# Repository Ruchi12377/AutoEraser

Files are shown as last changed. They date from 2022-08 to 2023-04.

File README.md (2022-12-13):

# 自動ホワイトボード消しの実用化に向けた改良

## 2022/12/13 第4版発行

---

# 目次

1. はじめに
   
   1. 概要
   
   2. 開発環境
   
   3. システムの概要

2. コンポーネント
   
   1. Camera
   
   2. Image
   
   3. KeystoneCorrection
   
   4. WhiteBoard (Feature)
   
   5. Select
   
   6. Erase (Feature)
   
   7. MoveInitial
   
   8. InitialSetting
   
   9. Pump
   
   10. Move (Feature)
   
   11. Serial

# 1.はじめに

## 1.概要

我々はRTミドルウェアを用いて、ホワイトボードの文字を自動で消すシステムを開発している。本稿では、本システムの改善について述べる。昨年のシステムとの相違点は主に三点ある。一つ目は、材質を木材からアルミニウムに変更することで歪みを解消し、スムーズな可動と軽量化を図ったことである。二つ目は消したい領域をより細かく指定可能にすることで、本来消すべきではない部分を消してしまうことを防げるようになったことである。三つ目は水が入ったタンクを設置し、自動で白板を濡らすことができるようになったため、雑巾を取り外して濡らす必要がなくなったことである。

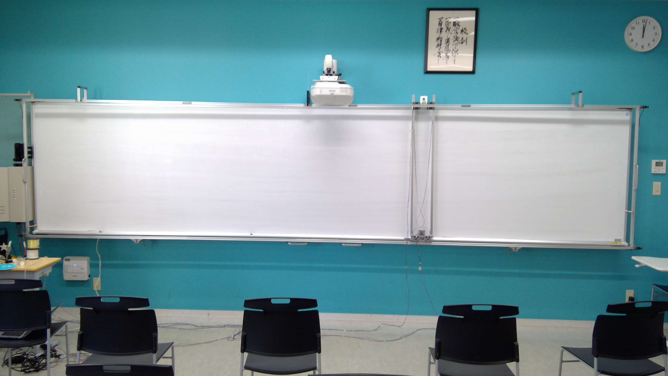
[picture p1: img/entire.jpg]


自動ホワイトボード消しのイメージ

## 2.開発環境

本コンポーネント群の開発環境を以下に示す。

| OS | Windows10 |
| --- | --- |
| RTミドルウェア | OpenRTM-aist-2.0.0-RELESE(Python 版) |
| 開発環境 | VSCode |
| Python | 3.8.5 |
| 必要モジュール  | math, numpy, cv2, PIL, sys, time, tkinter |

## 3.システムの概要

このシステムは、ユーザーの指定した範囲もしくは、全範囲(全部消す)をレールや枠組みに沿って本体が移動し自動でホワイトボードに書かれたものを消すものである。

そして、制御部分にはRTミドルウェアを用いており、Cameraコンポーネントを用いて取得したホワイトボードの動画(画像)をSelectコンポーネントで消す範囲を選択し、Eraseコンポーネントでどのように移動するか決定することでMoveコンポーネントが移動するためのコマンドを生成し、Serialコンポーネントを用いてハードウェアに移動するデータをもちいて実際に動かす。というものである。

以下の2つのコンポーネント図を示す。

1.詳しく説明してあるコンポーネント図

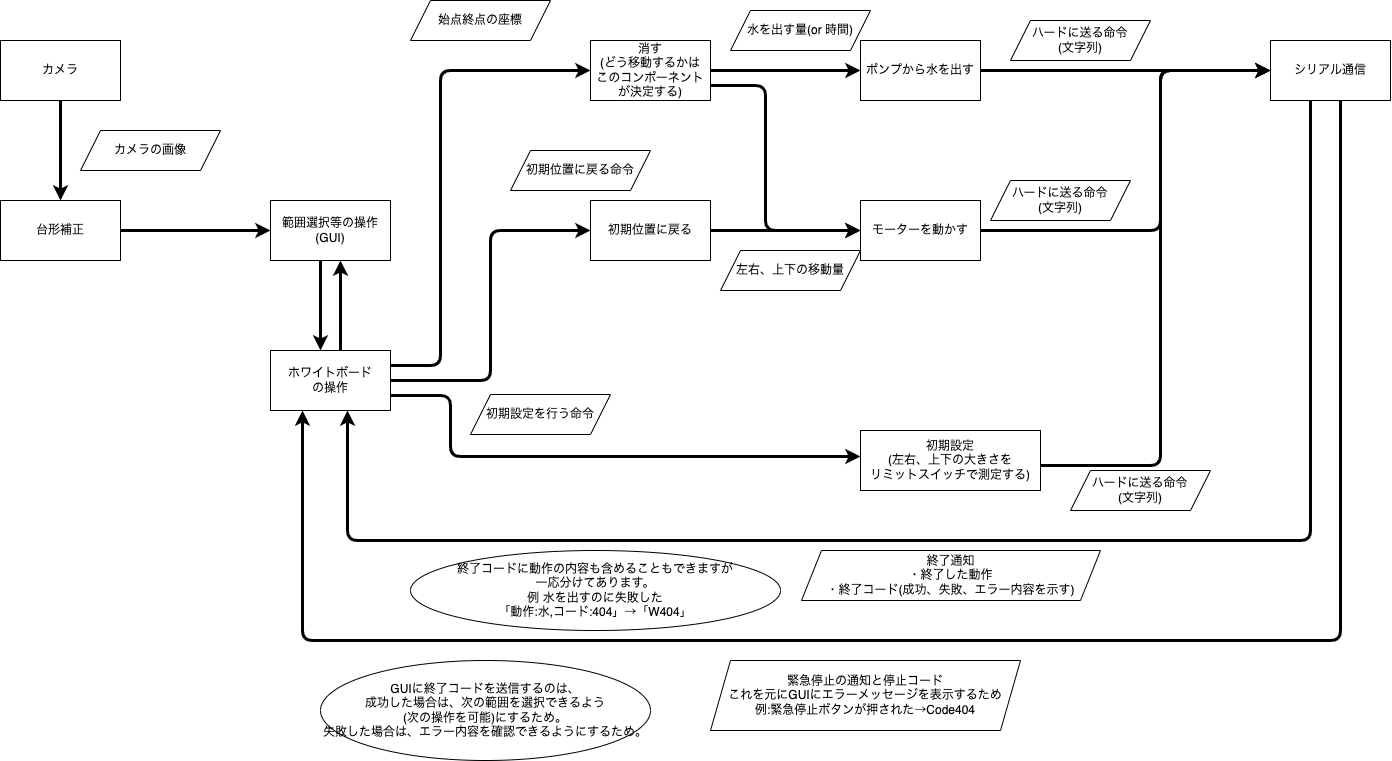
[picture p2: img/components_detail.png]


2.簡潔化しまとまりごとに色分けしたコンポーネント図

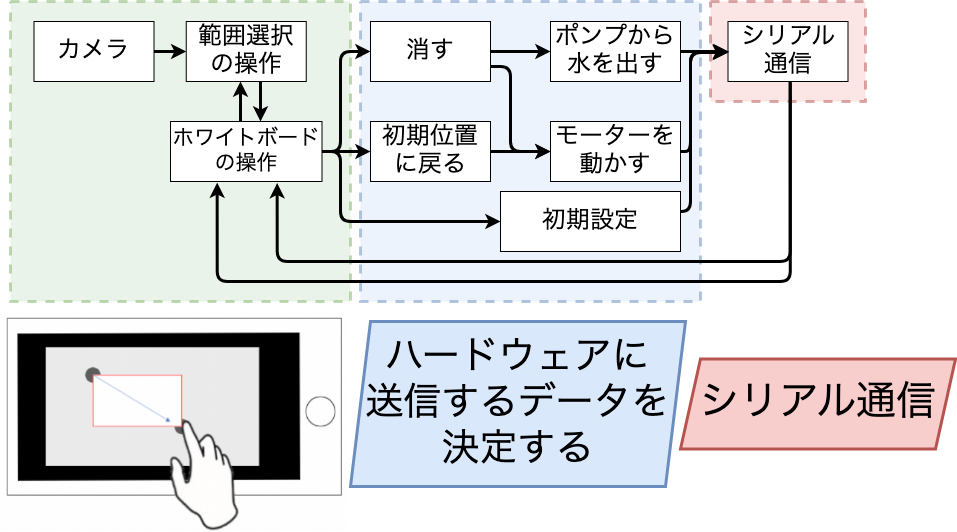
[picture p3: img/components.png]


# 2.コンポーネント

## 1.Camera

カメラから取得した画像を出力するコンポーネント。

コンフィギュレーションから使用するカメラのインデックスを設定することができる。

- **InPort**

- **OutPort**
  
  | **名称** | **データ型**         | **説明**            |
  | ------ | ---------------- | ----------------- |
  | image  | RTC::CameraImage | カメラから取得した画像を出力する。 |

- Configuration
  
  | 名称          | データ型  | 説明                   | 初期値 | 制限      |
  | ----------- | ----- | -------------------- | --- | ------- |
  | CameraIndex | short | 使用するカメラのインデックスを設定する。 | 0   | 0<=x<=5 |

## 2.Image

コンフィギュレーションで指定されたパスの画像をポートから出力するコンポーネント。

デバックする際、Cameraコンポーネントの代わりに使用することを想定している。

- **InPort**

- **OutPort**
  
  | 名称    | データ型             | 説明                           |
  | ----- | ---------------- | ---------------------------- |
  | Image | RTC::CameraImage | コンフィギュレーションで指定されたパスの画像を出力する。 |

- **Configuration**
  
  | 名称   | データ型   | 説明        | 初期値          | 制限        |
  | ---- | ------ | --------- | ------------ | --------- |
  | Path | string | 出力する画像のパス | Emprt String | Undefined |

## 3.KeystoneCorrection

台形補正をするコンポーネント。

GUIに画像が表示されており、4隅をクリックすることで台形補正を行う。

ホワイトボードをカメラで撮影しなぞるようにして選択するが、その際ホワイトボードの画像は斜めになっているのでこのコンポーネントが必要。

- **InPort**

| 名称 | データ型 | 説明 |
| --- | --- | --- |
| ImageIn | RTC::CameraImage | 台形補正をする画像 |

- **OutPort**

| 名称 | データ型 | 説明 |
| --- | --- | --- |
| ImageOut | RTC::CameraImage | 台形補正済みの画像 |

- **Configuration**

## 4.WhiteBoard (Feature)

実装予定

## 5.Select

範囲選択をし、選択した矩形の座標を出力するコンポーネント。

選択範囲を左上を基準とし0~1で表す。真ん中から右下まで選択した場合、Start = (0.5, 0.5) End = (1, 1)となる。

**Camera** **Image** **Select** の3つに加え画像切り取りコンポーネントを作成することで画像切り取りができるコンポーネント群をかんたんに作れる。

- **InPort**
  
  | 名称            | データ型        | 説明          |
  | ------------- | ----------- | ----------- |
  | ShowImage     | CameraImage | 選択する際の背景の画像 |
  | CompeteMotion | TimedString | 終了した動作名     |
  | StatusCode    | TimedUShort | ステータスコード    |

- **OutPort**
  
  | 名称       | データ型              | 説明         |
  | -------- | ----------------- | ---------- |
  | StartPos | RTC::TimedPoint2D | 指定された範囲の始点 |
  | EndPos   | RTC::TimedPoint2D | 指定された範囲の終点 |

- **Configuration**
  
  | 名称     | データ型 | 説明         | 初期値 | 制限           |
  | ------ | ---- | ---------- | --- | ------------ |
  | Width  | int  | 選択ウィンドウの横幅 | 800 | 400<=x<=1600 |
  | Height | int  | 選択ウィンドウの高さ | 450 | 225<=x<=900  |

## 5.Erase (Feature)

選択された範囲を元に消すためのパスを決定するコンポーネント。

- **InPort**
  
  | 名称       | データ型              | 説明         |
  | -------- | ----------------- | ---------- |
  | StartPos | RTC::TimedPoint2D | 指定された範囲の始点 |
  | EndPos   | RTC::TimedPoint2D | 指定された範囲の終点 |

- **OutPort**
  
  | 名称       | データ型           | 説明                         |
  | -------- | -------------- | -------------------------- |
  | MovePath | TimedStringSeq | **x:y**の形式で移動する座標のデータを出力する |

- **Configuration**
  
  | 名称  | データ型 | 説明  | 初期値 | 制限  |
  | --- | ---- | --- | --- | --- |
  |     |      |     |     |     |

## 5.MoveInitial

初期位置(左上)に本体を移動させるコンポーネント。

移動しきったかの検出にはリミットスイッチを用いる。

- **InPort**
  
  | 名称            | データ型      | 説明              |
  | ------------- | --------- | --------------- |
  | MoveToInitial | RTC::Time | 初期位置に戻るタイミングを指定 |

- **OutPort**
  
  | 名称      | データ型             | 説明                |
  | ------- | ---------------- | ----------------- |
  | Command | RTC::TimedString | 初期位置に戻るためのコマンドを生成 |

- **Configuration**
  
  | 名称      | データ型 | 説明               | 初期値 | 制限        |
  | ------- | ---- | ---------------- | --- | --------- |
  | TimeOut | int  | 移動完了せずタイムアウトする時間 | -1  | -1<=x<=60 |

## 6.InitialSetting

本体のサイズ、ホワイトボードの横幅をリミットスイッチを用いて検出するコンポーネント。

単位はステッピングモーターの回転数。

- **InPort**
  
  | 名称      | データ型      | 説明        |
  | ------- | --------- | --------- |
  | Setting | RTC::Time | 検出するタイミング |

- **OutPort**
  
  | 名称      | データ型             | 説明                |
  | ------- | ---------------- | ----------------- |
  | Command | RTC::TimedString | 初期設定を行うためのコマンドを生成 |

- **Configuration**
  
  | 名称  | データ型 | 説明  | 初期値 | 制限  |
  | --- | ---- | --- | --- | --- |
  |     |      |     |     |     |

## 7.Pump

指定された量の水をポンプから出すコンポーネント。

単位はmL

- **InPort**
  
  | 名称          | データ型             | 説明         |
  | ----------- | ---------------- | ---------- |
  | WaterAmount | RTC::TimedUShort | ポンプから出す水の量 |

- **OutPort**
  
  | 名称              | データ型             | 説明               |
  | --------------- | ---------------- | ---------------- |
  | PumpWaterAmount | RTC::TimedString | ポンプから水を出すためのコマンド |

- **Configuration**
  
  | 名称   | データ型 | 説明  | 初期値 | 制限  |
  | ---- | ---- | --- | --- | --- |
  | Amou |      |     |     |     |

## 8.Move (Feature)

パスを元に、モーターを動かすためのコマンドを生成するコンポーネント。

- **InPort**
  
  | 名称      | データ型              | 説明            |
  | ------- | ----------------- | ------------- |
  | Command | RTC::TimedPoint2D | モーターを動かすための座標 |

- **OutPort**
  
  | 名称      | データ型             | 説明              |
  | ------- | ---------------- | --------------- |
  | Command | RTC::TimedString | ハードウェアに送信するコマンド |

- **Configuration**
  
  | 名称  | データ型 | 説明  | 初期値 | 制限  |
  | --- | ---- | --- | --- | --- |
  |     |      |     |     |     |

## 9.Serial

シリアル通信のRead/Writeを行うコンポーネント。

- **InPort**
  
  | 名称    | データ型             | 説明             |
  | ----- | ---------------- | -------------- |
  | Write | RTC::TimedString | シリアル通信で書き込むデータ |

- **OutPort**
  
  | 名称   | データ型             | 説明              |
  | ---- | ---------------- | --------------- |
  | Read | RTC::TimedString | シリアル通信で読み込んだデータ |

- **Configuration**
  
  | 名称        | データ型   | 説明               | 初期値         | 制限        |
  | --------- | ------ | ---------------- | ----------- | --------- |
  | Path      | string | シリアル通信を行うデバイスのパス | EmptyString |           |
  | Boundrate | int    | シリアル通信を行うための速度   | 9600        | Undefined |

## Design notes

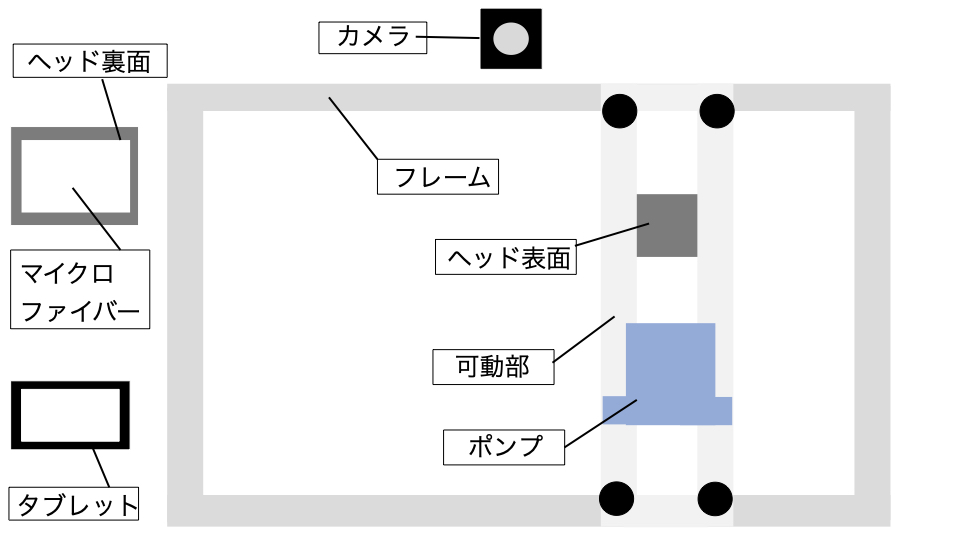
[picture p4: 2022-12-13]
img/structure/s1.jpeg

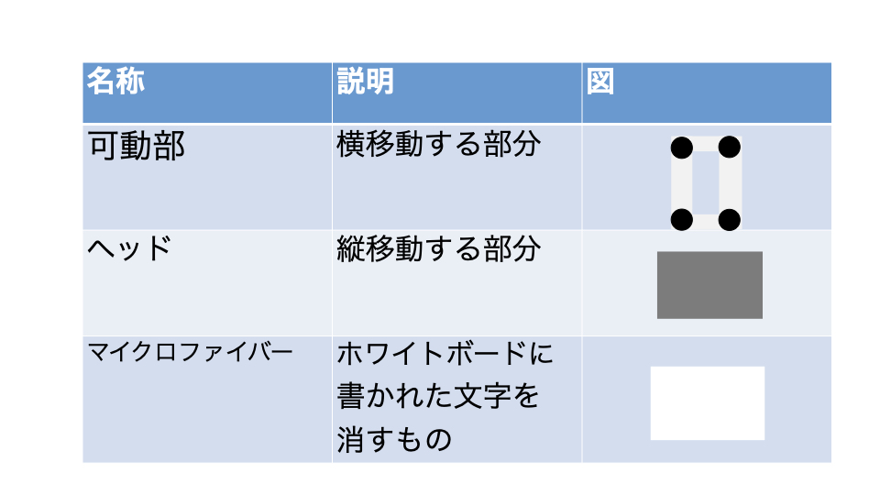
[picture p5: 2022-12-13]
img/structure/s3.jpeg

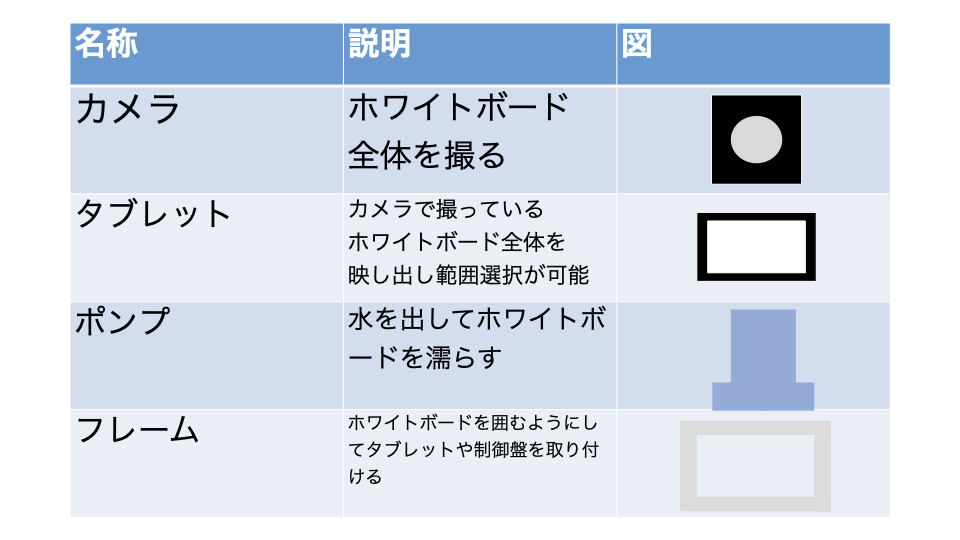
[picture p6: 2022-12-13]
img/structure/s2.jpeg

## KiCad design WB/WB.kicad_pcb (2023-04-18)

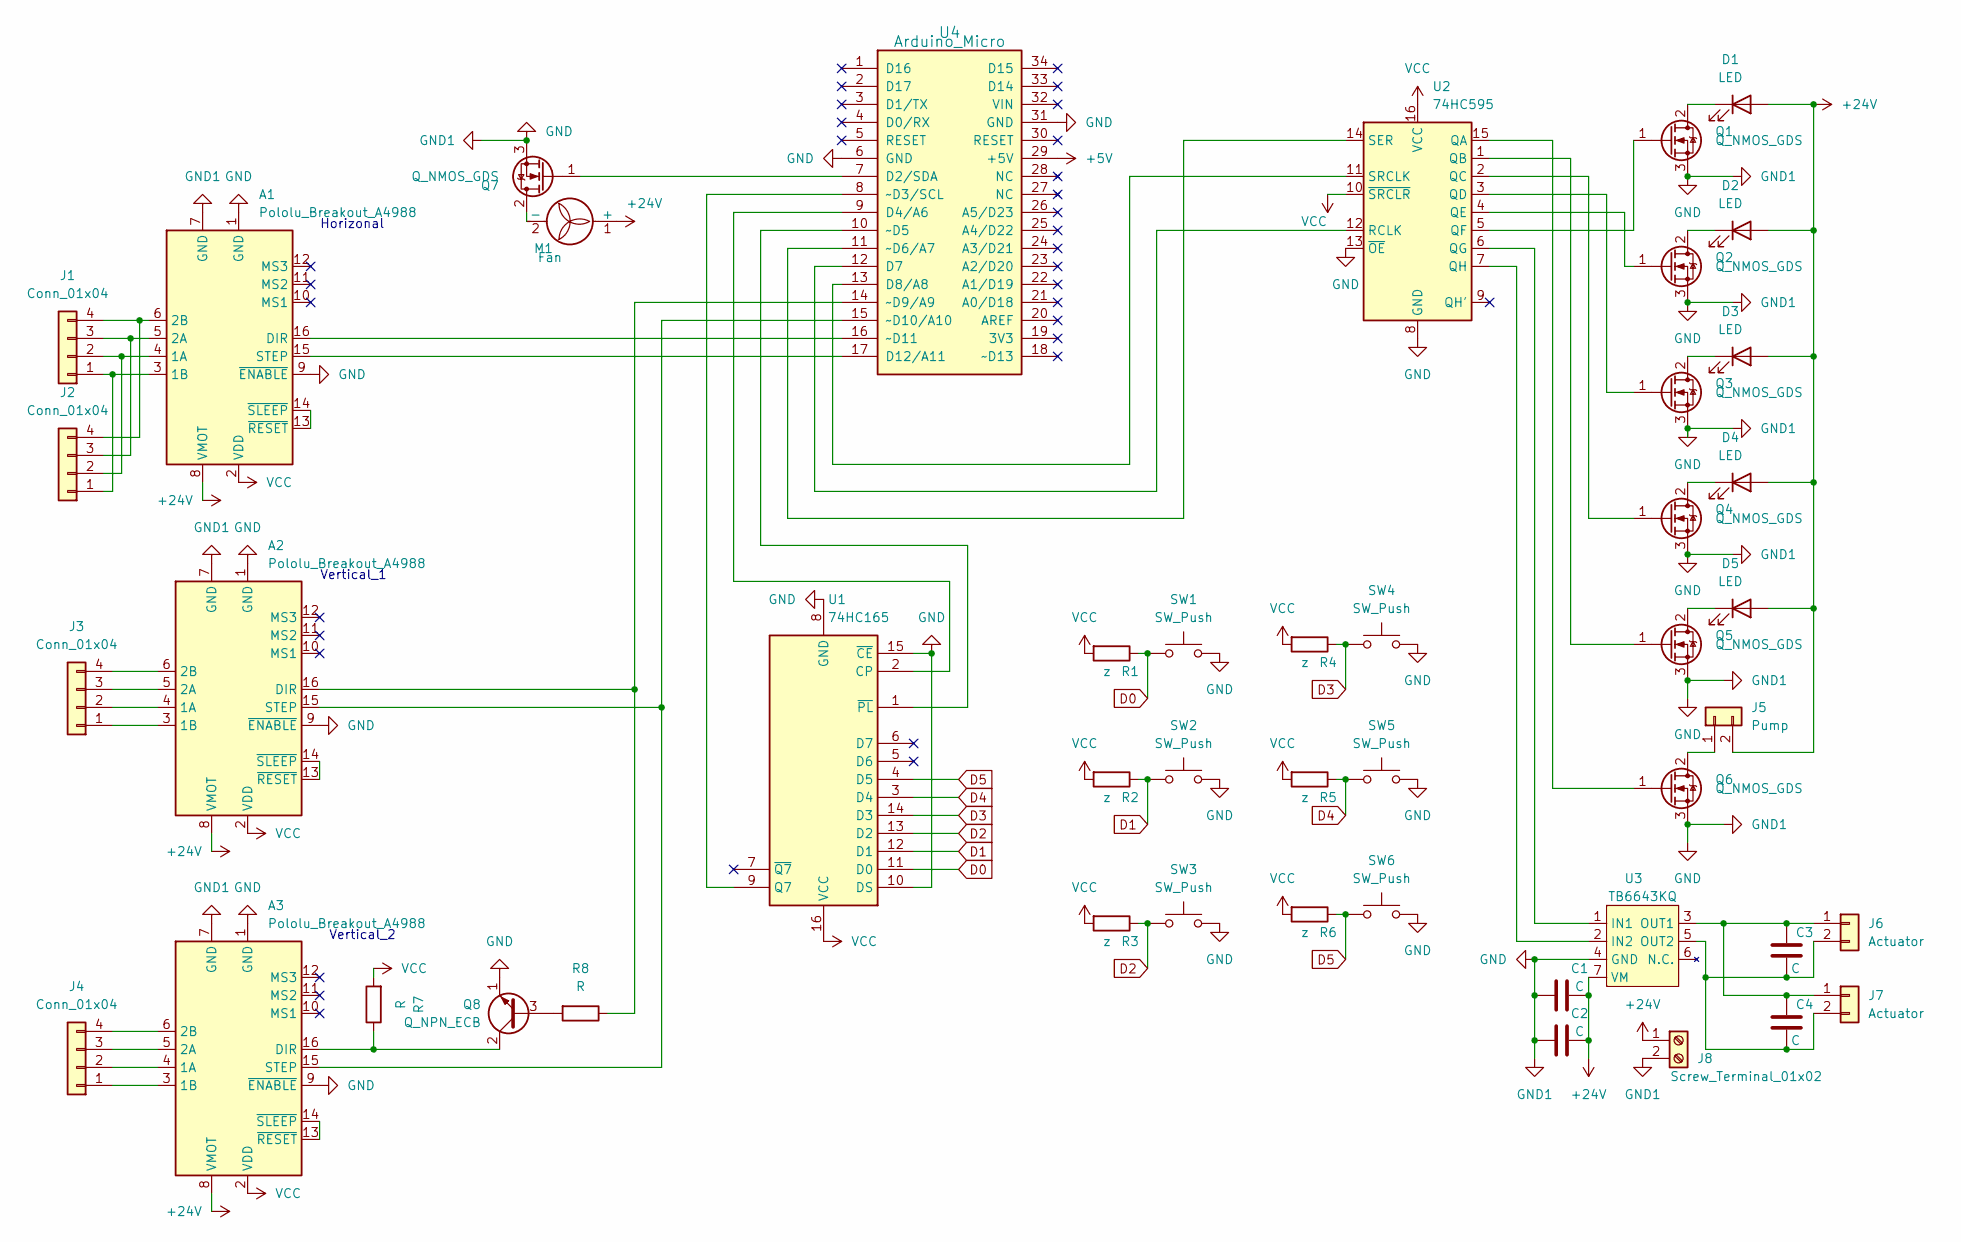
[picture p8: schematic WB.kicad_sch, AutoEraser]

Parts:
A1, A2, A3: Pololu_Breakout_A4988; MODULE_A4988_STEPPER_MOTOR_DRIVER_CARRIER
C1, C3, C4: C; C_Rect_L4.0mm_W2.5mm_P2.50mm
C2: C; C_Radial_D8.0mm_H11.5mm_P3.50mm
D1, D2, D3, D4, D5: LED; PinHeader_1x02_P2.54mm_Vertical
J1, J2, J3, J4: Conn_01x04; PinHeader_1x04_P2.54mm_Vertical
J5: Pump; PinHeader_1x02_P2.54mm_Vertical
J6, J7: Actuator; PinHeader_1x02_P2.54mm_Vertical
J8: Screw_Terminal_01x02; TerminalBlock_bornier-2_P5.08mm
M1: Fan; PinHeader_1x02_P2.54mm_Vertical
Q1, Q2, Q3, Q4, Q5, Q6, Q7: Q_NMOS_GDS; TO254P1054X470X1955-3
Q8: Q_NPN_ECB; TO-92L_Inline_Wide
R1, R2, R3, R4, R5, R6: z; R_Box_L8.4mm_W2.5mm_P5.08mm
R7, R8: R; R_Box_L8.4mm_W2.5mm_P5.08mm
SW1, SW2, SW3, SW4, SW5, SW6: SW_Push; PinHeader_1x02_P2.54mm_Vertical
U1: 74HC165; DIP-16_W7.62mm
U2: 74HC595; DIP-16_W7.62mm
U3: TB6643KQ; SIP1005W50P254L1965H1265Q7
U4: Arduino_Micro

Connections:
+24V: A1.8 (VMOT), A2.8 (VMOT), A3.8 (VMOT), C1.2, C2.2, D1.2 (A), D2.2 (A), D3.2 (A), D4.2 (A), D5.2 (A), J5.2, J8.1, M1.1 (+), U3.7 (VM)
D0: R1.1, SW1.1, U1.11 (D0)
D1: R2.1, SW2.1, U1.12 (D1)
D2: R3.1, SW3.1, U1.13 (D2)
D3: R4.1, SW4.1, U1.14 (D3)
D4: R5.1, SW5.1, U1.3 (D4)
D5: R6.1, SW6.1, U1.4 (D5)
GND: A1.1 (GND), A1.7 (GND), A2.1 (GND), A2.7 (GND), A2.9 (~ENABLE), A3.1 (GND), A3.7 (GND), A3.9 (~ENABLE), C1.1, C2.1, J8.2, Q1.3 (S), Q2.3 (S), Q3.3 (S), Q4.3 (S), Q5.3 (S), Q6.3 (S), Q7.3 (S), Q8.1 (E), SW1.2, SW2.2, SW3.2, SW4.2, SW5.2, SW6.2, U1.8 (GND), U1.10 (DS), U1.15 (~CE), U2.8 (GND), U2.13 (~OE), U3.4 (GND), U4.6 (GND), U4.31 (GND); also elsewhere on the board
unnamed: A1.3 (1B), J1.1, J2.1
unnamed: A1.4 (1A), J1.2, J2.2
unnamed: A1.5 (2A), J1.3, J2.3
unnamed: A1.6 (2B), J1.4, J2.4
unnamed 12: A1.9 (~ENABLE); also elsewhere on the board
unnamed: A1.13 (~RESET), A1.14 (~SLEEP)
unnamed 14: A1.15 (STEP), U4.17 (D12/A11); also elsewhere on the board
unnamed 15: A1.16 (DIR), U4.16 (~D11); also elsewhere on the board
unnamed: A2.3 (1B), J3.1
unnamed: A2.4 (1A), J3.2
unnamed: A2.5 (2A), J3.3
unnamed: A2.6 (2B), J3.4
unnamed: A2.13 (~RESET), A2.14 (~SLEEP)
unnamed 21: A2.15 (STEP), A3.15 (STEP), U4.15 (~D10/A10); also elsewhere on the board
unnamed 22: A2.16 (DIR), R8.1, U4.14 (~D9/A9); also elsewhere on the board
unnamed: A3.3 (1B), J4.1
unnamed: A3.4 (1A), J4.2
unnamed: A3.5 (2A), J4.3
unnamed: A3.6 (2B), J4.4
unnamed: A3.13 (~RESET), A3.14 (~SLEEP)
unnamed: A3.16 (DIR), Q8.2 (C), R7.1
unnamed: D1.1 (K), Q1.2 (D)
unnamed: D2.1 (K), Q2.2 (D)
unnamed: D3.1 (K), Q3.2 (D)
unnamed: D4.1 (K), Q4.2 (D)
unnamed: D5.1 (K), Q5.2 (D)
unnamed: J5.1, Q6.2 (D)
unnamed: C3.1, C4.1, J6.1, J7.1, U3.3 (OUT1)
unnamed: C3.2, C4.2, J6.2, J7.2, U3.5 (OUT2)
unnamed: M1.2 (-), Q7.2 (D)
unnamed: Q1.1 (G), U2.5 (QF)
unnamed: Q2.1 (G), U2.4 (QE)
unnamed: Q3.1 (G), U2.3 (QD)
unnamed: Q4.1 (G), U2.2 (QC)
unnamed: Q5.1 (G), U2.1 (QB)
unnamed: Q6.1 (G), U2.15 (QA)
unnamed: Q7.1 (G), U4.7 (D2/SDA)
unnamed: Q8.3 (B), R8.2
unnamed: U1.1 (~PL), U4.10 (~D5)
unnamed: U1.2 (CP), U4.9 (D4/A6)
unnamed: U1.9 (Q7), U4.8 (~D3/SCL)
unnamed: U2.6 (QG), U3.1 (IN1)
unnamed: U2.7 (QH), U3.2 (IN2)
unnamed: U2.11 (SRCLK), U4.13 (D8/A8)
unnamed: U2.12 (RCLK), U4.12 (D7)
unnamed: U2.14 (SER), U4.11 (~D6/A7)
VCC: A1.2 (VDD), A2.2 (VDD), A3.2 (VDD), R1.2, R2.2, R3.2, R4.2, R5.2, R6.2, R7.2, U1.16 (VCC), U2.10 (~SRCLR), U2.16 (VCC); also elsewhere on the board

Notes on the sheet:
Vertical_2
Vertical_1
Horizonal

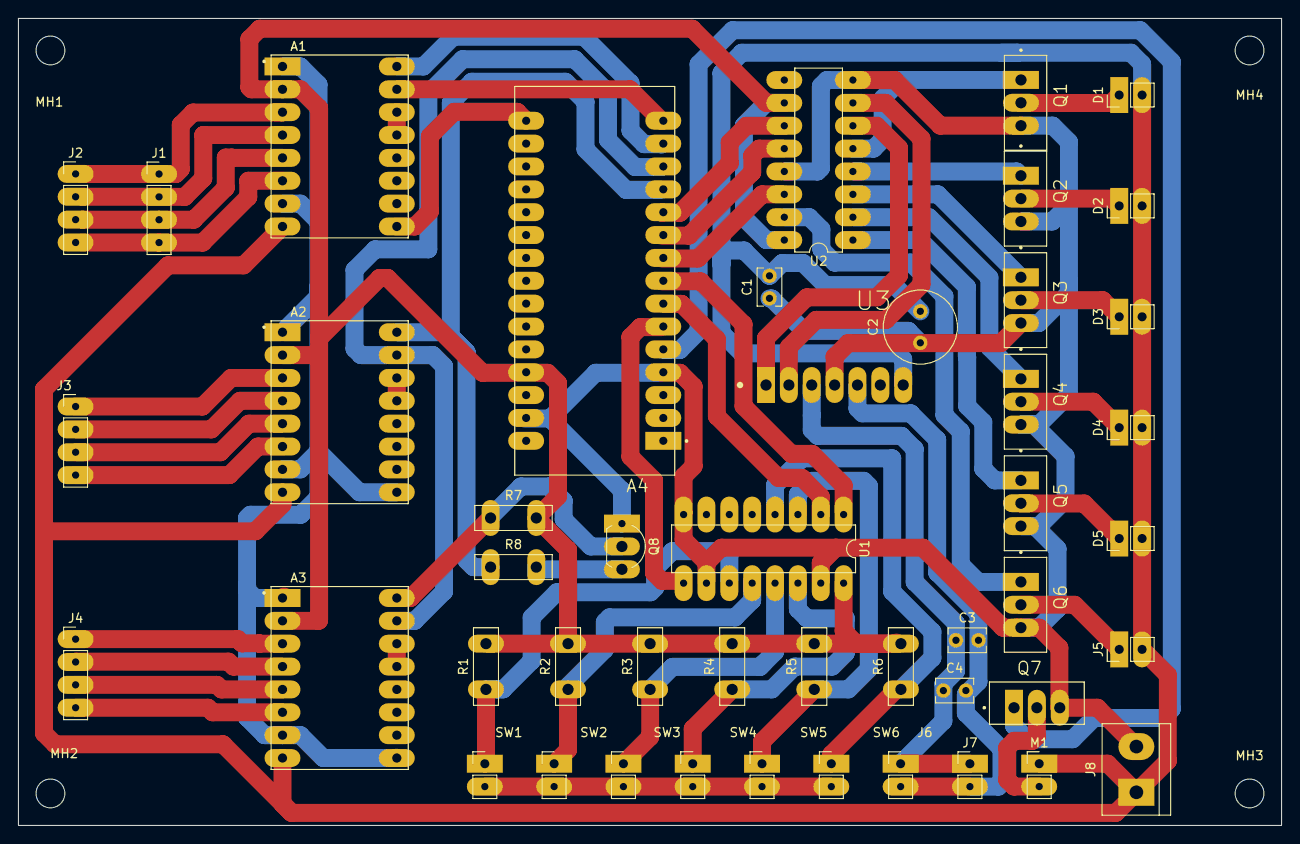
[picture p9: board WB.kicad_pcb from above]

Board: 2 copper layers, 140.3 x 89.7 mm, 51 parts (0 on the bottom side), 48 nets.

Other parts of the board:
A4: Arduino_Micro; SHIELD_ARDUINO_NANO
MH1, MH2, MH3, MH4: MountingHole_3.2mm_M3

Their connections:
GND: A4.4 (GND), A4.29 (GND); also elsewhere on the board
unnamed 12: A4.16 (D13); also elsewhere on the board
unnamed 14: A4.15 (D12); also elsewhere on the board
unnamed 15: A4.14 (D11); also elsewhere on the board
unnamed 21: A4.13 (D10); also elsewhere on the board
unnamed 22: A4.12 (D9); also elsewhere on the board
VCC: A4.27 (+5V); also elsewhere on the board

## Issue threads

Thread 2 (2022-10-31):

消すコンポーネントの追加

Ruchi12377, 2022-10-31:

Ruchi12377, 2022-11-18:
https://github.com/Ruchi12377/AutoEraser/commit/1d052e3bd791cab6dc2d7d45511b62dff50d2dd4
https://github.com/Ruchi12377/AutoEraser/commit/136b809391789d1ab055eebd52357854f6d0d64e
https://github.com/Ruchi12377/AutoEraser/commit/9ab25b67a1e6541ea8d078a88ba658b7350a35a2
https://github.com/Ruchi12377/AutoEraser/commit/3cdded5868a3584b9529b3162f4c081dcfbba398
https://github.com/Ruchi12377/AutoEraser/commit/11bdb302ad065de05a7d6524006aaecdd41a70f7

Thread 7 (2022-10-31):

簡略化したコンポーネント図の訂正

Ruchi12377, 2022-10-31:

Ruchi12377, 2022-10-31:
シリアル通信からカメラの矢印ではなく、シリアル通信から範囲選択に二つの矢印が正しい。
二つの矢印は終了通知とエラー通知

Ruchi12377, 2022-11-18:
https://github.com/Ruchi12377/AutoEraser/commit/f2b52287dd68b40760af7dd51279eeb14af9a9e5
https://github.com/Ruchi12377/AutoEraser/commit/ac9677ecf97e80e2aa6eaeac08b8d775e65b4243
https://github.com/Ruchi12377/AutoEraser/commit/8a261d6aac12c1226cdb6942a4902e6934316654
https://github.com/Ruchi12377/AutoEraser/commit/12d7879febcd1b47bad622e56bd53a834729cc52

Closed 2022-11-18.

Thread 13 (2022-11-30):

ハードウェアの構成について

Nobu19800, 2022-11-30:
自動ホワイトボード消しのシステムは、モーター、カメラ、水の入ったタンク等で構成されていますが、構成や動作が分かりづらいと思います。
例えば、「自動で白板を濡らす」というのが、どこから水が出て、全体を濡らすのか、部分的に濡らすのかが分かりません。

Ruchi12377, 2022-12-13:
https://github.com/Ruchi12377/AutoEraser/commit/c26e47882edf824ec0da6dec0e9ea834b52c910d
このコミットにて対応しました。

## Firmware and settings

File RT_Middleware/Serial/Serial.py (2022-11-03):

#!/usr/bin/env python
# -*- coding: utf-8 -*-
# -*- Python -*-

"""
 @file Serial.py
 @brief Serial communication
 @date $Date$


"""
import OpenRTM_aist
import RTC
import sys
import time
import serial
from serial.tools import list_ports
sys.path.append(".")

# Import RTM module


# Import Service implementation class
# <rtc-template block="service_impl">

# </rtc-template>

# Import Service stub modules
# <rtc-template block="consumer_import">
# </rtc-template>


# This module's spesification
# <rtc-template block="module_spec">
serial_spec = ["implementation_id", "Serial",
               "type_name",		 "Serial",
               "description",	   "Serial communication",
               "version",		   "1.0.0",
               "vendor",			"Ruchi",
               "category",		  "Category",
               "activity_type",	 "STATIC",
               "max_instance",	  "1",
               "language",		  "Python",
               "lang_type",		 "SCRIPT",
               "conf.default.Port", "COM3",
               "conf.default.Baudrate", "9600",

               "conf.__widget__.Port", "text",
               "conf.__widget__.Baudrate", "text",
               "conf.__constraints__.Baudrate", "x>0",

               "conf.__type__.Port", "string",
               "conf.__type__.Baudrate", "int",

               ""]
# </rtc-template>

##
# @class Serial
# @brief Serial communication
#
#


class Serial(OpenRTM_aist.DataFlowComponentBase):

    ##
    # @brief constructor
    # @param manager Maneger Object
    #
    def __init__(self, manager):
        OpenRTM_aist.DataFlowComponentBase.__init__(self, manager)

        self._d_wData = OpenRTM_aist.instantiateDataType(RTC.TimedString)
        """
		"""
        self._WriteIn = OpenRTM_aist.InPort("Write", self._d_wData)
        self._d_rData = OpenRTM_aist.instantiateDataType(RTC.TimedString)
        """
		"""
        self._ReadOut = OpenRTM_aist.OutPort("Read", self._d_rData)

        # initialize of configuration-data.
        # <rtc-template block="init_conf_param">
        """

		 - Name:  Port
		 - DefaultValue: COM3
		"""
        self._Port = ['COM3']
        """

		 - Name:  Baudrate
		 - DefaultValue: 9600
		"""
        self._Baudrate = [9600]

        # </rtc-template>

    ##
    #
    # The initialize action (on CREATED->ALIVE transition)
    # formaer rtc_init_entry()
    #
    # @return RTC::ReturnCode_t
    #
    #

    def onInitialize(self):
        # Bind variables and configuration variable
        self.bindParameter("Port", self._Port, "COM3")
        self.bindParameter("Baudrate", self._Baudrate, "9600")

        # Set InPort buffers
        self.addInPort("Write", self._WriteIn)

        # Set OutPort buffers
        self.addOutPort("Read", self._ReadOut)

        # Set service provider to Ports

        # Set service consumers to Ports

        # Set CORBA Service Ports

        return RTC.RTC_OK

    ###
    ##
    # The finalize action (on ALIVE->END transition)
    # formaer rtc_exiting_entry()
    ##
    # @return RTC::ReturnCode_t
    #
    ##
    # def onFinalize(self):
    #
    # return RTC.RTC_OK

    ###
    ##
    # The startup action when ExecutionContext startup
    # former rtc_starting_entry()
    ##
    # @param ec_id target ExecutionContext Id
    ##
    # @return RTC::ReturnCode_t
    ##
    ##
    # def onStartup(self, ec_id):
    #
    # return RTC.RTC_OK

    ###
    ##
    # The shutdown action when ExecutionContext stop
    # former rtc_stopping_entry()
    ##
    # @param ec_id target ExecutionContext Id
    ##
    # @return RTC::ReturnCode_t
    ##
    ##
    # def onShutdown(self, ec_id):
    #
    # return RTC.RTC_OK

    ##
    #
    # The activated action (Active state entry action)
    # former rtc_active_entry()
    #
    # @param ec_id target ExecutionContext Id
    #
    # @return RTC::ReturnCode_t
    #
    #
    def onActivated(self, ec_id):
        devices = [info.device for info in list_ports.comports()]
        # port is not found
        if ((self._Port[0] in devices) == False):
            print("port is not found :" + self._Port[0])
            print("please connect usb, or select a port below")
            for i in range(len(devices)):
                print("> " + devices[i])
            return RTC.RTC_OK

        self.ser = [serial.Serial()]
        self.ser[0].baudrate = self._Baudrate[0]
        self.ser[0].port = self._Port[0]
        self.ser[0].timeout = 1

        try:
            self.ser[0].open()
            print("port is opened : " + self._Port[0])
            return RTC.RTC_OK
        except:
            print("Can't open port : " + self._Port[0])

        return RTC.RTC_OK

    ##
    #
    # The deactivated action (Active state exit action)
    # former rtc_active_exit()
    #
    # @param ec_id target ExecutionContext Id
    #
    # @return RTC::ReturnCode_t
    #
    #
    def onDeactivated(self, ec_id):

        return RTC.RTC_OK

    ##
    #
    # The execution action that is invoked periodically
    # former rtc_active_do()
    #
    # @param ec_id target ExecutionContext Id
    #
    # @return RTC::ReturnCode_t
    #
    #
    def onExecute(self, ec_id):
        if (self._WriteIn.isNew()):
            self.ser[0].write(str.encode(self._WriteIn.read().data))

        return RTC.RTC_OK

    ###
    ##
    # The aborting action when main logic error occurred.
    # former rtc_aborting_entry()
    ##
    # @param ec_id target ExecutionContext Id
    ##
    # @return RTC::ReturnCode_t
    ##
    ##
    # def onAborting(self, ec_id):
    #
    # return RTC.RTC_OK

    ###
    ##
    # The error action in ERROR state
    # former rtc_error_do()
    ##
    # @param ec_id target ExecutionContext Id
    ##
    # @return RTC::ReturnCode_t
    ##
    ##
    # def onError(self, ec_id):
    #
    # return RTC.RTC_OK

    ###
    ##
    # The reset action that is invoked resetting
    # This is same but different the former rtc_init_entry()
    ##
    # @param ec_id target ExecutionContext Id
    ##
    # @return RTC::ReturnCode_t
    ##
    ##
    # def onReset(self, ec_id):
    #
    # return RTC.RTC_OK

    ###
    ##
    # The state update action that is invoked after onExecute() action
    # no corresponding operation exists in OpenRTm-aist-0.2.0
    ##
    # @param ec_id target ExecutionContext Id
    ##
    # @return RTC::ReturnCode_t
    ##

    ##
    # def onStateUpdate(self, ec_id):
    #
    # return RTC.RTC_OK

    ###
    ##
    # The action that is invoked when execution context's rate is changed
    # no corresponding operation exists in OpenRTm-aist-0.2.0
    ##
    # @param ec_id target ExecutionContext Id
    ##
    # @return RTC::ReturnCode_t
    ##
    ##
    # def onRateChanged(self, ec_id):
    #
    # return RTC.RTC_OK


def SerialInit(manager):
    profile = OpenRTM_aist.Properties(defaults_str=serial_spec)
    manager.registerFactory(profile,
                            Serial,
                            OpenRTM_aist.Delete)


def MyModuleInit(manager):
    SerialInit(manager)

    # Create a component
    comp = manager.createComponent("Serial")


def main():
    mgr = OpenRTM_aist.Manager.init(sys.argv)
    mgr.setModuleInitProc(MyModuleInit)
    mgr.activateManager()
    mgr.runManager()


if __name__ == "__main__":
    main()

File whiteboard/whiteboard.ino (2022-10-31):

#include <RStep.h>

RStep v = RStep(12, 11, 10, 1, 0, 1550);
RStep v2 = RStep(9, 8, 7, 0, 0, 1550);
RStep h = RStep(6, 5, 4, 1, 0, 1550);

int split(String data, char delimiter, String *dst){
    int index = 0;
    int arraySize = (sizeof(data)/sizeof((data)[0]));  
    int datalength = data.length();
    for (int i = 0; i < datalength; i++) {
        char tmp = data.charAt(i);
        if ( tmp == delimiter ) {
            index++;
            if ( index > (arraySize - 1)) return -1;
        }
        else dst[index] += tmp;
    }
    return (index + 1);
}
 
void setup()
{
  Serial.begin(9600);
  pinMode(13, OUTPUT);
}

void loop()
{
  digitalWrite(13, HIGH);
  delay(1000);
  digitalWrite(13, LOW);
  delay(1000);
  return;
  h.update();
  v.update();
  v2.update();

  while (Serial.available() != 0)
  {
    String str = Serial.readString();
    str.trim();
    if(str == "stop"){
      h.stop();
      v.stop();
      v2.stop();
    }

    String cmds[3] = {"\0"}; // 分割された文字列を格納する配列 
    int index = split(str, ':', cmds);
    long hNum = cmds[0].toInt();
    h.set(hNum);
    long vNum = cmds[1].toInt();
    v.set(vNum);
    v2.set(vNum);
  }
}

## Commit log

2022-08-07 Selectコンポーネントを作成
2022-08-07 コメントを追加
2022-08-21 bug fix
    deactivateした後にactivateするとエラーになるバグを修正
2022-10-23 重複部分を修正
2022-10-30 バージョン情報を追加
2022-10-31 Selectの説明
2022-10-31 ステッピングモーターライブラリ
2022-10-31 制御プログラム
2022-10-31 表を追加
2022-10-31 各コンポーネントの説明を追加
2022-10-31 目次を編集
2022-10-31 図の位置の変更と、各コンポーネント説明の文末を追加
2022-11-02 回路図を追加
    [WB.dsn, WB.kicad_pcb, WB.kicad_sch]
2022-11-02 Serialコンポーネントを追加
2022-11-02 バグ修正とバッチファイル
2022-11-03 Serial通信
2022-11-03 シリアル通信テスト用文字入力コンポーネント
2022-11-03 画像の追加とリンクを修正
2022-11-04 Selectのコードを再生成しバグ修正
2022-11-07 ファン、アクチュエーターを追加。配置を修正
    [WB-B_Cu.gbr, WB-B_Mask.gbr, WB-B_Paste.gbr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]
2022-11-08 配線の修正
    [WB.dsn, WB.kicad_pcb, WB.kicad_sch]
2022-11-08 ICのDIPを変更。
    [WB.dsn, WB.kicad_pcb, WB.kicad_sch]
2022-11-09 配線の太さを太く
    [WB-B_Cu.gbr, WB-B_Mask.gbr, WB-B_Paste.gbr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]
2022-11-09 不要なファイルの削除
2022-11-10 配線がかぶっていたところを修正
    [WB-B_Cu.gbr, WB-B_Mask.gbr, WB-B_Paste.gbr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]
2022-11-12 パッドのサイズを変更したが、だめ
    [WB-B_Cu.gbr, WB-B_Paste.gbr, WB-B_Silkscreen.gbr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]
2022-11-13 配線しやすいように回路を変更
    [WB.dsn, WB.kicad_pcb, WB.kicad_sch]
2022-11-17 メインマイコンの変更
    [WB.kicad_pcb, WB.kicad_sch]
2022-11-17 台形補正コンポーネント
2022-11-18 ホワイトボード操作コンポーネントを追加
2022-11-18 詳細のコンポーネント図の修正
2022-11-18 背景を透明に
2022-11-18 差し替え
2022-11-18 ポンプとmoveini
    ポンプとmoveini
2022-11-18 スペースや改行を修正
2022-11-18 コンポーネント図の修正。ホワイトボード操作コンポーネントの追加
2022-11-18 コンポーネント説明の追加
2022-12-05 バッチファイルの追加。不要ファイルの削除
2022-12-05 回路図の修正
    [WB.kicad_pcb, WB.kicad_sch]
2022-12-13 台形補正の修正
    台形補正の修正（変数名、フォーマット、コンフィグ変数）
2022-12-13 台形補正の修正の修正の修正
2022-12-13 説明文の追加
2022-12-13 台形補正の修正の以下略
2022-12-13 構成するものを図で表した
2023-04-18 回路周りのファイル
    [Cane.kicad_pcb, Cane.kicad_sch, Stick.kicad_pcb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]
